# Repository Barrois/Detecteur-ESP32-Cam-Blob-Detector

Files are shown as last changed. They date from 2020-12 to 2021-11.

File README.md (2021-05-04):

# Detecteur-ESP32-Cam : Blob Detector Localisator

## Découpe des tâches à effectuer

- [x] [Détection acoustique du vol du frelon asiatique](./sketchbook/ESP_CAM_Audio_Detection): Vespa Velutina Nigrithorax (ESP32-Cam).

- [x] Détection et prise de photo du frelon asiatique en vol stationnaire en moins d'une seconde (ESP32-Cam).

- [x] Localisation d'un Blob dans une photo JPEG/jpg en 180ms pour une résolution 320x240 pixels (ESP32-Cam).

- [x] Détection de la tâche la plus sombre de l'image (ESP32-Cam).

- [x] Déduction coordonnées/angles des servos pour actionner un pan/tilt (ESP32-Cam).

- [x] Transmission de l'ordre de déplacement du pan/tilt: un angle pour chacun des deux servos du pan/tilt (ESP32-Cam).

- [x] [Réception/écoute du port série](./sketchbook/CoordonneesSerie) pour récupérer les valeurs des angles (Arduino 3.3V)

- [x] Déplacement des servos alimentés et controllés par PCA9695 (Arduino 3.3V)

- [x] Écoute du capteur d'obstacle laser (Arduino 3.3V)

- [x] Actionnement d'une électrovanne via relais (Arduino 3.3V)

- [ ] Assembler les sections correspondantes dans un programme pour l'ESP32-Cam

- [ ] Assembler les sections correspondantes dans un programme pour l'Arduino

- [ ] Tester en conditions réelles

- [ ] Corriger/adapter/améliorer/pleurer :D

## Présentation du projet

Après analyse des fréquences émises lors du vol stationnaire du frelon devant une ruche,
nous avons mis au point un filtre FFT qui donne satisfaction puisqu'il a permis de détecter des frelons dans 5 sites différents en France durant l'été 2020 : Limoux, Limoges, Toulouse, Nice et Caen.

Afin de valider le filtre acoustique, nous avons réalisé un programme s'executant sur un ESP32-Cam muni d'un micro (sur son unique entrée dispo ou presque: GPIO0) pour faire un photo de l'intrus, cette détection s'effectue en moins d'une seconde.

La prise de la photo, son analyse pour déduire la localisation du frelon est quant à elle réalisée en moins de 300ms (nb: en direct par l'ESP32-CAM).

### Principe d'analyse de l'image

L' analyse de la photo est basée sur le contraste et la taille d'une zone sombre (blob):

- La photo est prise depuis le dessus de la ruche en plongée devant un écran blanc.

- Les frelons, les abeilles et les résidus parsèment la photo et le pixel le plus noir n'est pas forcement la cible.

Toutefois en agglomérant des blocs de 4x4 pixels, on obtient des blobs dont le plus sombre est possiblement notre frelon:
plus gros qu'une abeille et plus noir/sombre qu'une feuille.

### Action !
Les coordonnées sont déduites de l'image et sont transmises à un Pan-Tilt guidé par un Arduino et équipé d'un dispositif de riposte (bille, eau, laser ...).

Il y a deux solutions en cours de recherche :

1.  Un ESP32-CAM détecte acoustiquement le Frelon asiatique, prend la photo en 320x240, l'analyse et transmet les coordonnées à un Arduino qui anime un Pan-Tilt équipé d'un laser. Actuellement c'est la solution explorée, la détection prend moins d'une seconde et la localisation 300ms.

2. un ESP32 équipé d'un Shield OV7670 et d'un Shield SD, détecte le frelon, prend la photo en 80x60, l'analyse et anime le Pan-Tilt équipé du laser.

Ce qui est fait :

- [x] la détection
- [x] la prise de photo
- [x] l'analyse et la localisation en pixel dans la photo

- [x] La détection par FFT et la sauvegarde sur carte SD : [ESP_CAM_timelapse_detector_Etienne_0.ino](./sketchbook/ESP_CAM_timelapse_detector_Etienne_0/ESP_CAM_timelapse_detector_Etienne_0.ino)

- [x] L'analyse en partant des photos mises en mémoires SPIFFS et la localisation du Blob : [decoder_jpeg_08_1.ino](./sketchbook/decoder_jpeg_08_1/decoder_jpeg_08_1.ino)

- [x] La prise de photo et l'analyse de blob grâce à l'excellent EloquentArduino :
https://github.com/eloquentarduino/EloquentArduino

et son example : https://eloquentarduino.github.io/2020/01/motion-detection-with-esp32-cam-only-arduino-version/

- [x] Une détection d'un blob 4x4 dans une photo 320x240 en 180ms !!! = : ESP32CameraNaiveMotionDetection_1.ino
- [x] envoyer et recevoir les coordonnées  de l'[ESP32-CAM à l'Arduino via Tx-Rx](./sketchbook/ESP_CAM_Audio_Detection)

Ce qu'il reste à faire :

- [ ] déclencher le tir du laser 10W alimenté en 12v 5A !!!
- [x] sauver la photo avec les coordonnées du tir pour la postérité.

La logique actuellement est la suivante :
- quand on allume l'esp32-cam
  1. il lit l'EEProm pour savoir à quel numéro de fichier il en est : xxx
  2. il fait une localisation qu'il sauvegarde sur la carte SD : fichier LOCAxxx.txt
  3. il fait une photo sauvegardée sur la carte SD : fichier CAPTURExxx.jpg
  4. il se met en position d'écoute sur le port 0
  5. il fait la FFT
  6. si le filtre de la FFT est positif, il commence à compter
  7. si le compteur du filtre atteint 5 reconnaissances en moins d'une seconde
        il collecte les 5 FFT qui ont déclenchées l'alarme et les stocke sur la carte SD : fichier FFTxxx.txt
        puis l'esp32-cam redémarre pour faire la localisation et la photo
  8. sinon il recommence en -4

Cette nouvelle version ["ESP_CAM_detector_localisor_Patrick_0_1"](./sketchbook/ESP_CAM_detector_localisor_Patrick_0_1/ESP_CAM_detector_localisor_Patrick_0_1.ino) (en hommage à Patrick DESSEAUX qui m'aide beaucoup)
marque un tournant dans la détection : après son analyse, seule la première harmonique est testée : 230Hz +/- 10%.

Et sans doute allons-nous modifier aussi le dispositif suivant son idée : un micro sur le devant de la ruche et un micro d'ambiance,
afin de supprimer les faux positifs dus à l'environnement (mobylette et autres..) et donc raccourcir le temps de détection.

## Le canon à bille de Ptilab: la solution la plus prometteuse !

Un canon a été experimenté avec succés par Ptitlab et son ami bbruno:

Depuis 2017 ils tirent le frelon :  https://drive.google.com/file/d/16ssjIsU98TqoQO_uRPv50JdfcAjg1aXl/view?usp=sharing

Plus de renseignements sur : http://ruchewarre.net/viewtopic.php?f=175&t=10218
Nous attendons beaucoup de cette collaboration.

Si vous avez des idées pour tuer les frelons asiatiques, merci de nous en faire part

Merci à tous

# Documentation

## Composants

[Liste des composants](documentation/Composants.md)

## Schema des connexions ESP32-Cam

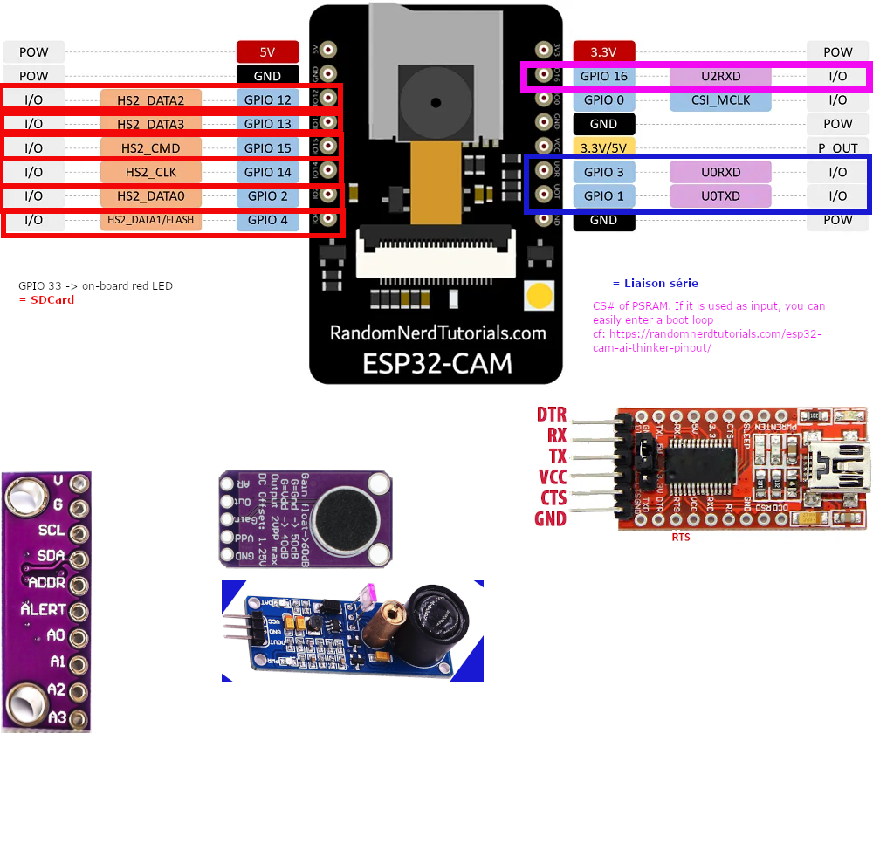
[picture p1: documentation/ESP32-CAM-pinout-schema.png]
SP32-CAM-pinout-schema


## Essais laser
[Essais laser](documentation/Laser.md)

## Quelques images capturées

### Frelons
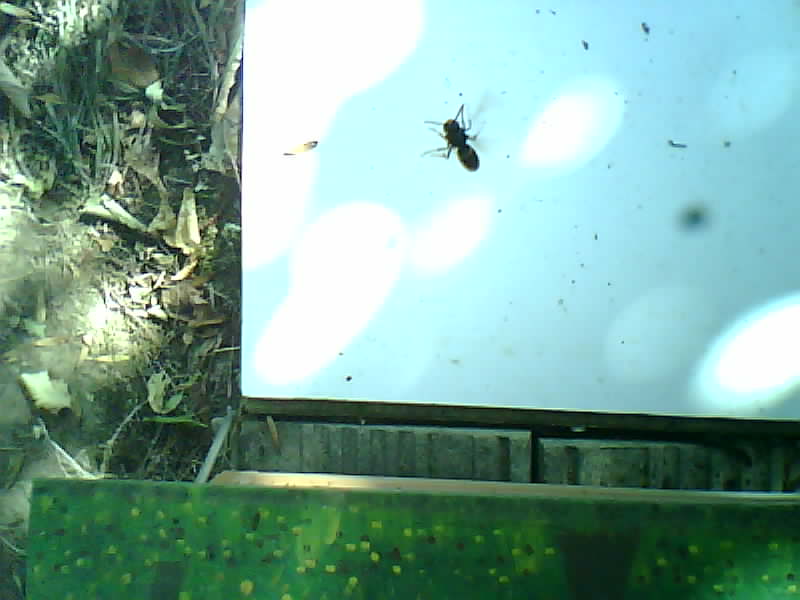
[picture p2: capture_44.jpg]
capture_44

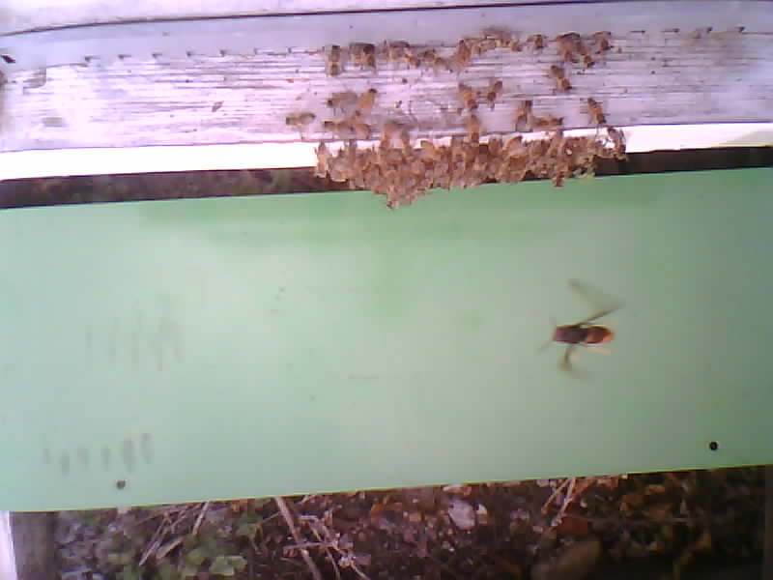
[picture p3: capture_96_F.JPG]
capture_96_F

capture_96_F

### Frelon ?
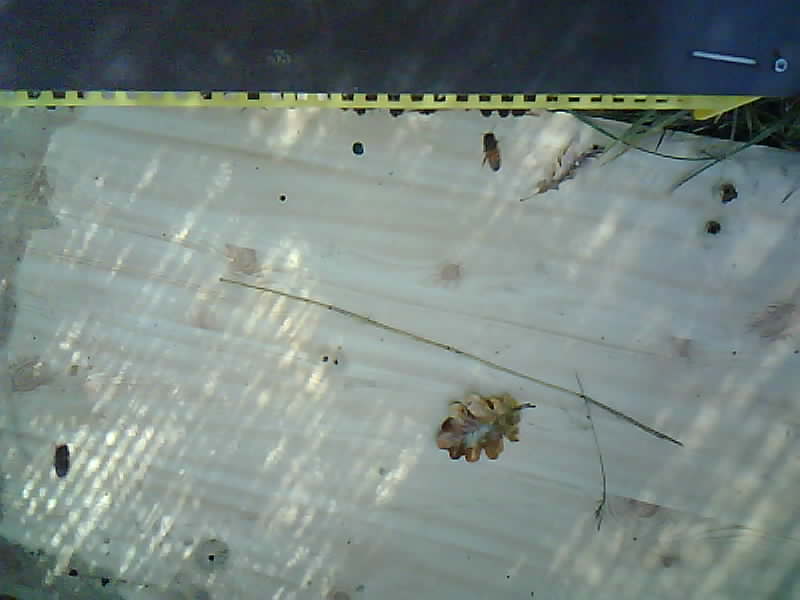
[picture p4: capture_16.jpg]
capture_16

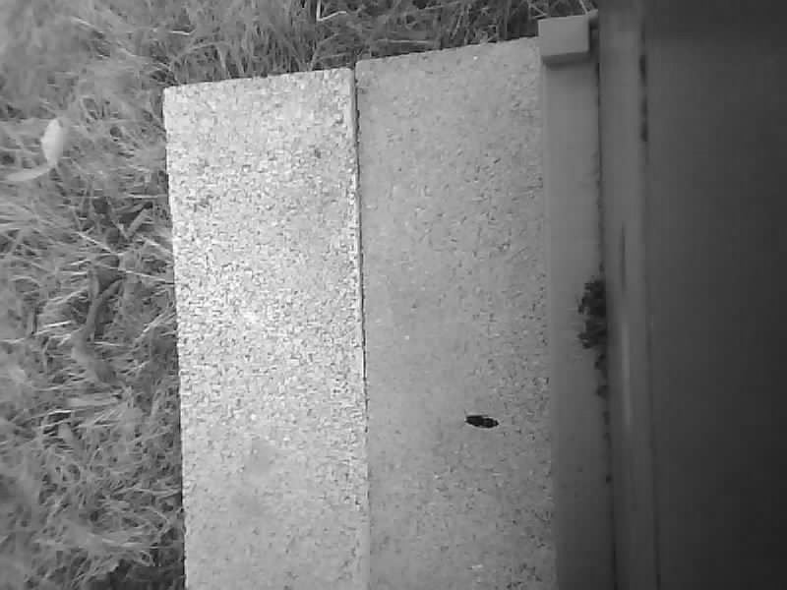
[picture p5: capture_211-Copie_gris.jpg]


## Enregistrements audio

[bruit_rue+frelon_1](Son-2019-08-16-09-39_bruit_rue+frelon_1.wav)

[bruit_rue+frelon_2](Son-2019-08-16-09-39_bruit_rue+frelon_2.wav)

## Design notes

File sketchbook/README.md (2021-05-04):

# Sketches de test

## Détection acoustique du vol de frelon

[Communication série](./CoordonneesSerie) de l'ESP32 vers Arduino (test côté Arduino)

[ESP_CAM_Audio_Detection](./ESP_CAM_Audio_Detection)

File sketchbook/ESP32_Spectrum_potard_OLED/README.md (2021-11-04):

# Détecteur acoustique de frelon pour ESP32

L'objectif est de faire un détecteur bas coût avec la possibilité d'ajuster la détection en fonction du frelon asiatique.
En effet le poids et la taille du frelon asiatique varient avec l'avancée de la saison et l'abondance de la nourriture,
ce qui entraine des variations du pic de détection qu'il faut pouvoir régler in situ, d'ou ce montage avec un potentiomètre.
L'affichage sur un écran permet de visualiser les valeurs de la fréquence la plus élevée (pic), celle du potentiomètre ainsi
qu'un message lors d'une détection.

## Pré requis

- Installation de la carte ESP32 dans l'IDE Arduino (cf: https://randomnerdtutorials.com/installing-the-esp32-board-in-arduino-ide-windows-instructions/)
- Installation de la librairie ArduinoFFT (https://github.com/kosme/arduinoFFT) depuis le getionnaire de librairies de l'IDE Arduino
- Installation de la librairie Adafruit_GFX_Library (Affichage écran OLED)
- Installation de la librairie Adafruit_SSD1306 (Affichage écran OLED)

## Raccordements

- le potentiomètre de règlage de la valeur du pic de fréquence est relié au GPIO 32, ADC1_CH4 (cf: potardPin 32)

- le micro (ici type MAX9814) est relié sur le GPIO 33, ADC1_CH5 (cf: microPIN 33)

- un écran OLED de 128x32 pixels en I2C sur GPIO 26 (PIN_SDA) et GPIO 27 (PIN_SCL);

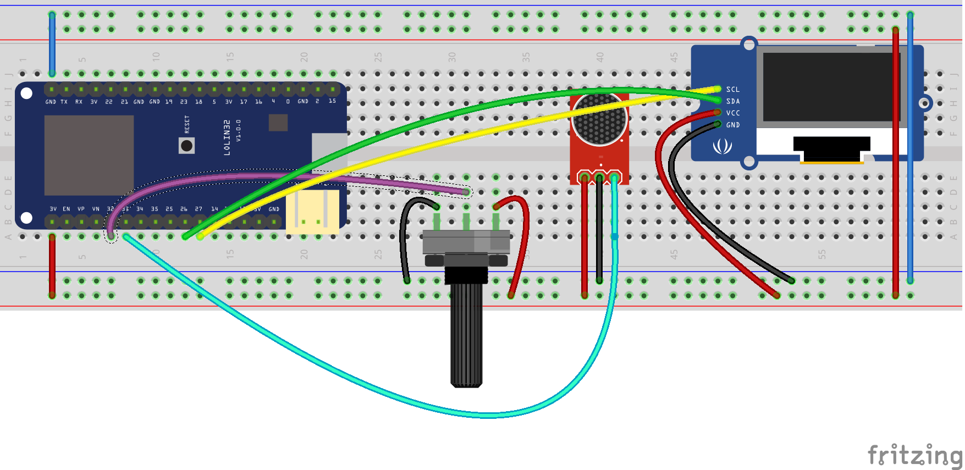
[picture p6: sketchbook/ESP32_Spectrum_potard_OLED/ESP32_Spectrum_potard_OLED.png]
Schema Breadboard

## Détection

Le potentiomètre permet de varier de 100 à 1000 Hz la fréquence de détection.

cf ligne 103, 4095 étant la valeur maximale de l'ADC, 100 correspond à 0 et 1000 à 4095:
```
int range = map(adc0, 0, 4095, 100, 1000);
```

la féquence de référence devrait se situer aux alentours de 230.

Il semblerait toutefois que les harmoniques soient plus facilement détectables.

Sans avoir vraiment d'explication, la fréquence 460 fonctionne mieux avec l'esp8266 que 230, et 920 pour l'ESP32.

À vérifier en "conditions réelles".

En cas de détection la led de la carte est allumée (variable LED_BUILTIN qui doit dépendre du type de carte sélectionnée dans l'IDE Arduino > Outils > Type de carte).

Sur l'ESP32 Lolin32 Lite servant aux essais, la logique est inversée: HIGH éteint la led et LOW l'allume, il faudra peut être inverser la logique sur une autre carte.

## Fichier de test

https://github.com/Jodaille/VespaVelutinaAudioRecords/blob/main/complets/2020-09-23-092858.ogg?raw=true

Avec 920 de valeur, en écoutant via un PC et Audacity en ajustant un peu le niveau, le frelon est détecté. Après le Koutish de la raquette de badmington, le frelon est au sol battant des ailes, la détection tout de même :-)

d'autres fichiers sont disponibles:

https://github.com/Jodaille/VespaVelutinaAudioRecords/tree/main/complets

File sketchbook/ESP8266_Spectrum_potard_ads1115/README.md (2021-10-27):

# Détecteur acoustique de frelon pour ESP8266

L'objectif est de faire un détecteur bas coût avec la possibilité d'ajuster la détection en fonction du frelon asiatique.
En effet le poids et la taille du frelon asiatique varient avec l'avancée de la saison et l'abondance de la nourriture,
ce qui entraine des variations du pic de détection qu'il faut pouvoir régler in situ, d'ou ce montage avec un potentiomètre

## Pré requis

- Installation de la carte ESP8266 dans l'IDE Arduino (cf: https://randomnerdtutorials.com/how-to-install-esp8266-board-arduino-ide/)
- Installation de la librairie ArduinoFFT (https://github.com/kosme/arduinoFFT) depuis le getionnaire de librairies de l'IDE Arduino
- Installation de la librairie Adafruit_ADS1X15 https://github.com/adafruit/Adafruit_ADS1X15

## Raccordements

- le micro est relié au seul ADC de l'esp8266, à savoir ADC0/A0
- le relais est relié sur la sortie D1, sauf que D1 est aussi SCL de l'I2C (D2 pour SDA)
il ne peut donc être enfiché directement sur les headers de l'ESP8266
- l'ESP8266 ne dispose que d'un ADC (A0), pour utiliser le potentiomètre de règlage de la valeur du pic de fréquence, nous utilisons un ADS1115 en I2C (D1 et D2)

## Schéma breadboard avec Fritzing

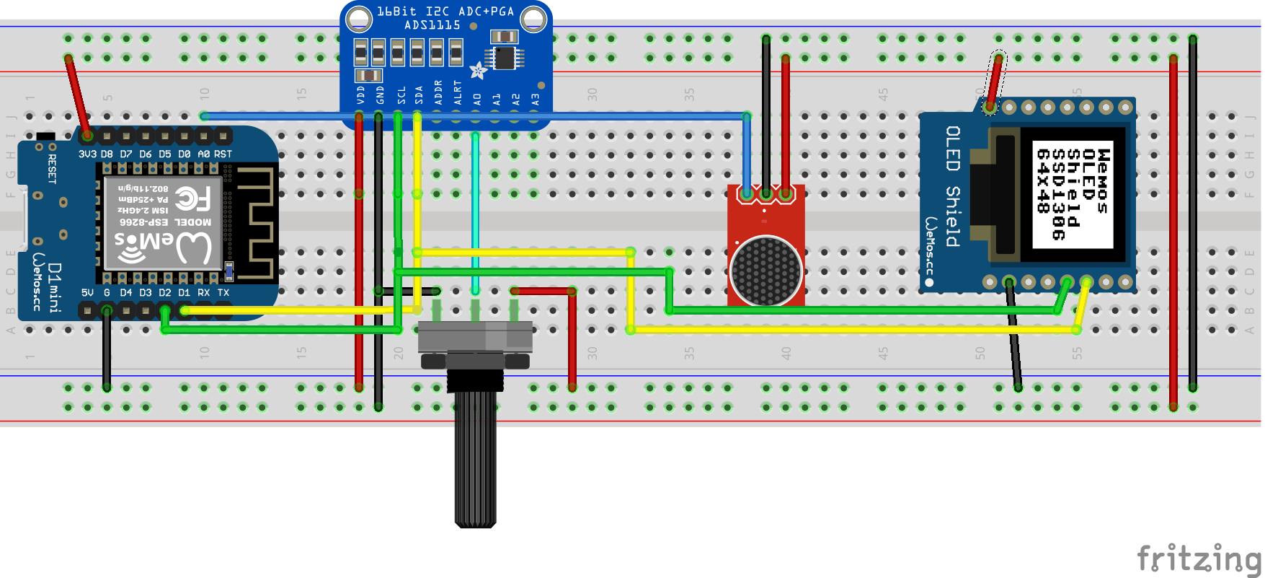
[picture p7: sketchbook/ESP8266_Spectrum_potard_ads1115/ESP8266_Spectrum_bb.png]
Schema Breadboard


Le circuit de test sur breadboard :
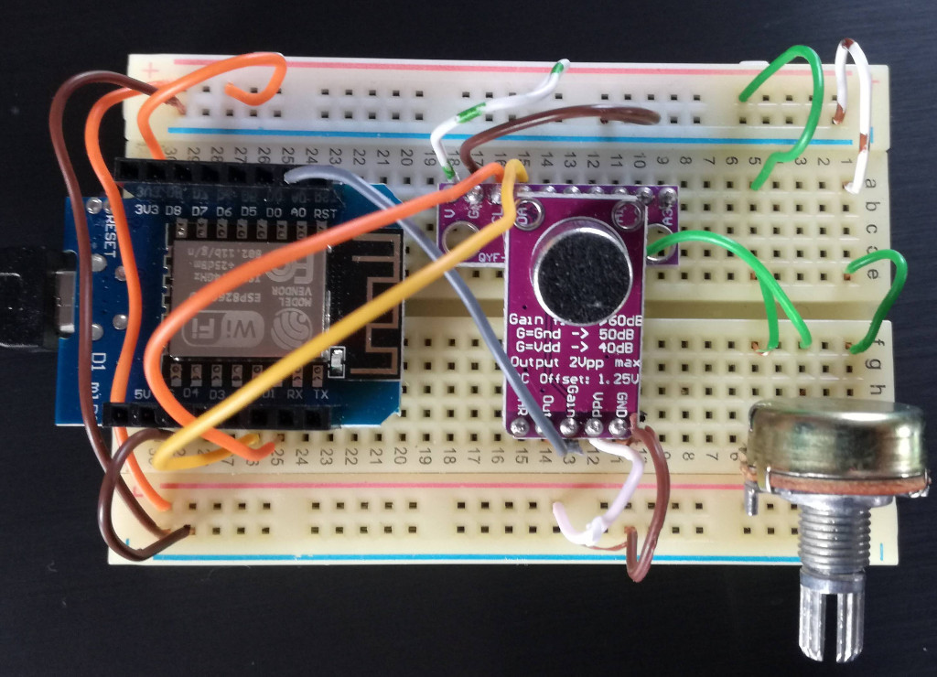
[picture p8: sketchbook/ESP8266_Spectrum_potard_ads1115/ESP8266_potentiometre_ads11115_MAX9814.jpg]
Circuit sur Breadboard


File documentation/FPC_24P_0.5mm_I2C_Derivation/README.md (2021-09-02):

# Déviation du bus I2C de l'Esp32-Cam avec deux plaques FPC 24P 0.5mm

Utilisation de headers mâles 2.54mm

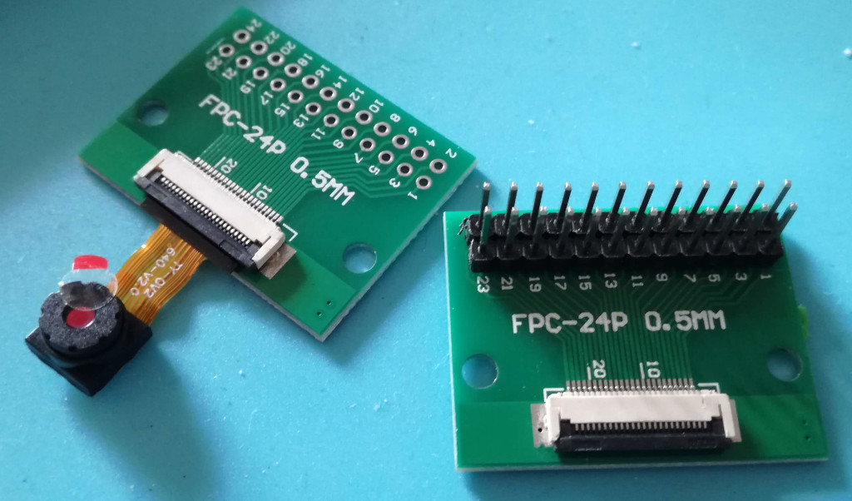
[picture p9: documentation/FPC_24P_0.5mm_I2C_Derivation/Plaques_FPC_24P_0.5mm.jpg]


Les deux plaques FPC 24P 0.5mm assemblées:

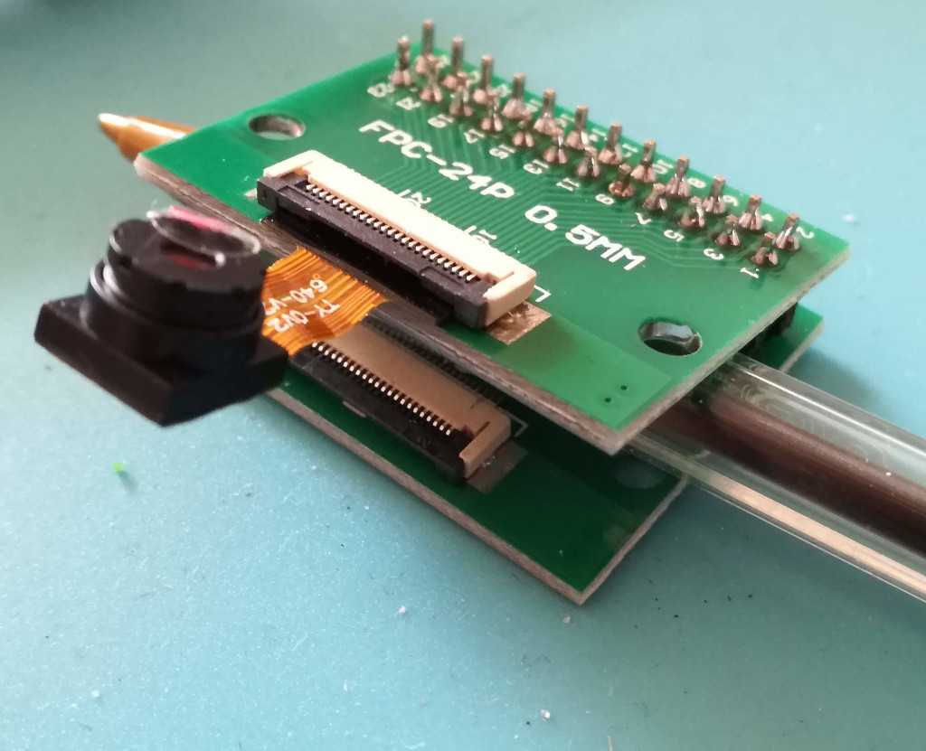
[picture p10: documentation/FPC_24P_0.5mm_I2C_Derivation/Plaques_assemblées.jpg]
Plaques assemblées Deux plaques FPC assemblées


Les plaques, la nappe, la caméra et l'ESP32-Cam

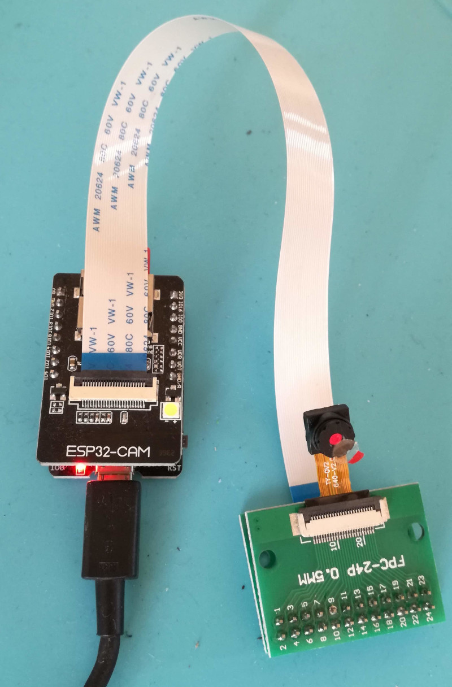
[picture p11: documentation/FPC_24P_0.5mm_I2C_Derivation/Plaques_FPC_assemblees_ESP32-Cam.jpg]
Les plaques, la nappe, la caméra et l'ESP32-Cam


Les connecteurs pour l'I2C:

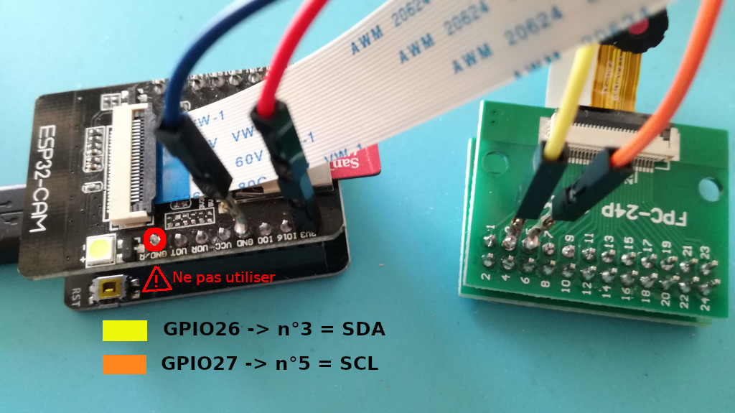
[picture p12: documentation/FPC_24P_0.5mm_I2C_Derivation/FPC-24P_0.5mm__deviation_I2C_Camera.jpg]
schéma SDA et SCL


## Exemple d'utilisation du bus I2C: scanner

```
#include <Wire.h>

const int PIN_SDA = 26;  // port 26 du esp32-cam sur le SDA directement sur la puce
const int PIN_SCL = 27;  // port 27 du esp32-cam sur le SCL directement sur la puce
void setup()
{
  Serial.begin(115200);
  Wire.begin(PIN_SDA, PIN_SCL);
}

void loop()
{
  byte error, address;
  int nDevices;

  Serial.println("Scanning...");

  nDevices = 0;
  for(address = 1; address < 127; address++ ) {
    // The i2c_scanner uses the return value of
    // the Write.endTransmisstion to see if
    // a device did acknowledge to the address.
    Wire.beginTransmission(address);
    error = Wire.endTransmission();

    if (error == 0) {
      Serial.print("I2C device found at address 0x");
      if (address<16) {
        Serial.print("0");
      }
      Serial.print(address,HEX);
      Serial.println("  !");
      nDevices++;
    }
    else if (error==4) {
      Serial.print("Unknow error at address 0x");
      if (address<16){
        Serial.print("0");
      }
      Serial.println(address,HEX);
    }
  }
  if (nDevices == 0) {
    Serial.println("No I2C devices found\n");
  }
  else {
    Serial.println("done\n");
  }
  delay(5000);           // wait 5 seconds for next scan
}
```

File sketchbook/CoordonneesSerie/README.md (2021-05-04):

# Test de passage de paramètres via le port série

## Utilisation de la virgule en tant que délimiteur

Afin de pouvoir indiquer les angles X (pan) et Y (tilt) aux deux servos,

nous projetons d'écrire ces coordonnées sur le port série depuis l'ESP32 vers l'Arduino.

Example pour X à 125° et Y à 145°
````
Serial.println("125,145")
````

## Passage d'un id de commande

Pour permettre un ajout d'autres paramètres (dans le futur), ou d'une autre action.

Nous ajoutons en premier paramètre un id de commande, la valeur 1 sera "déplacement des servos"

ainsi l'ESP32 enverra en premier la valeur 1, pour un ordre type "déplacement de servos":

Example pour X à 125° et Y à 145°
````
Serial.println("1,125,145")
````

## Tester depuis le moniteur série

Une fois le sketch chargé, il est possible de tester en indiquant dans le moniteur série, dans le prompt en haut de la fenêtre la chaîne de caractère suivante, suivi d'une validation par la touche Entrée:

````
1,24,67
````

le message en retour devrait être:

````
captured String is : 1,24,67
command = 1 / angleX = 24 / integerAngleX = 24
integerCommand = 1 / angleY = 67 / integerAngleY = 67
Deplacement du servo !
````

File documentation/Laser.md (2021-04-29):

# Laser ou pas laser

## Essais d'un laser

5.5w haute puissance 445NM focalisation module laser bleu gravure laser et découpe module TTL tube laser 5500mw

Description du produit :

- Longueur d'onde: 445NM
- Puissance: 5.5W (max. 4.8w)
- Courant électrique: entrée 3-5A
- Tension: DC 12V
- Température de fonctionnement: + 10 ~ + 40
- Module de pilote: TTL
- Mise au point Laser réglable
- Taille: 33*33*75mm

Possible de brûler du bois à près de 80cm en ajustant la "focale" (pas sûr du terne)

Toutefois pas d'instantaéité, il faut laisser le faisceau quelques secondes pour brûler.

En calant à peu près la focale (lorsqu'elle brûle du bois), j'ai essayé de toucher une grosse mouche,
celle-ci s'est envolée à peine en contact avec le faisceau.

## Pour

- Pas de projectile à ramasser

- Pas de projectile à recharger/débloquer

## Contre
- Illégalité: https://www.ecologie.gouv.fr/lutte-contre-lusage-des-lasers-dans-transport-aerien

- risque d'incendie

- risque de brûlure notamment des yeux !

- consommation électrique

- efficacité non démontrée

## Illustration

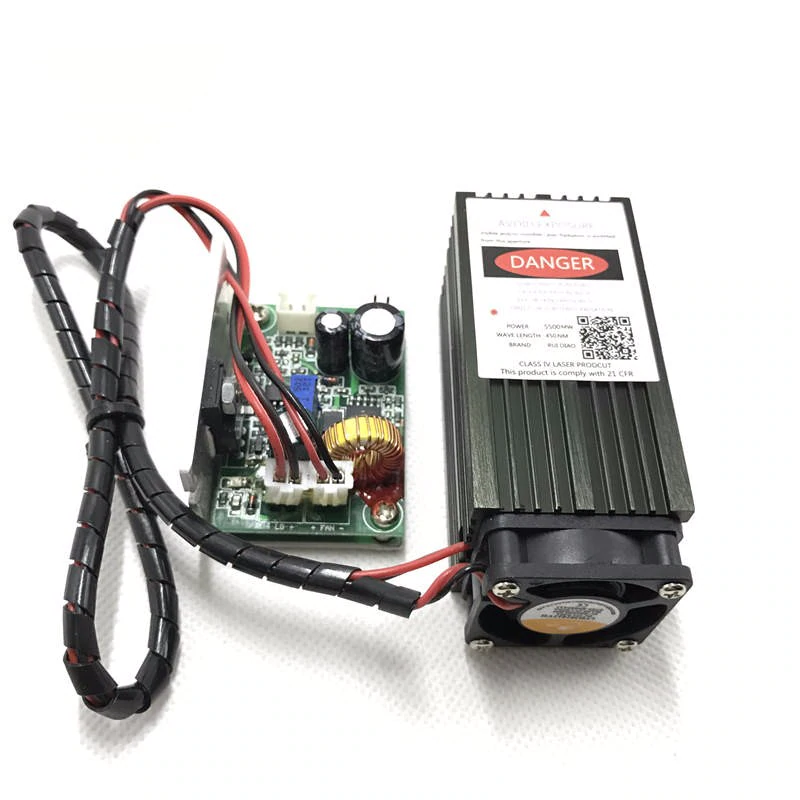
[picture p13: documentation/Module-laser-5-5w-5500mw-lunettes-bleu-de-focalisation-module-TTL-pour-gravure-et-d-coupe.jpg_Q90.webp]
module-laser-5-5w-5500mw


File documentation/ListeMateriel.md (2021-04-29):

Voici le matériel requis pour faire la partie détection-localisation

    un esp32-cam (objectif standard)
    une carte mémoire micro SD
    un module de chargement FTDI ou équivalent
    un micro MAX9814 ou équivalent (fabriqué par Michel) mais qui ne génére pas de GND sur le port zéro de l'esp32-Cam au départ
    une alimentation 5 volts 1A (2 c'est mieux)

Voici le matériel requis pour faire la partie canon (à air et bille ou à liquide, électromagnétique à clou ou goupille)

    un canon tel que désiré : à air et bille ou à liquide, électromagnétique à clou ou goupille
        pour le canon à air prévoir les électrovannes, les tuyaux, et la réserve d'air (vase d'expansion par exemple)
        et le STL de la culasse utilisé.
        pour le canon à liquide prévoir ... ce qu'il faut ... vanne, tuyau, etc...
        et le STL de la culasse utilisé.
        pour le canon électromagnétique prévoir l'alimentation spécifique à la bobine et son condensateur
        et le STL de la culasse utilisé.
    un Pan-Tilt
    deux servo-moteur 5V costauds pour la maneouvre du canon
    un servo-moteur 5V pour la gachette du canon ou l'armenemt suivant le cas
    une relais 12V pour les électrovannes si nécessaire
    un PCA9685 pour gérer les servo-moteurs et leur alimentation
    un viseur électronique : module LASER d'Adafruit ou son équivalent fabriqué par Michel
    un arduino mini pro ou nano de préférence en 3.3 volts
    un ads1115 (facultatif)
    un écran Oled (facultatif)
    une alimentation 5 volts 2A pour l'arduino
    une alimentation 12v pour les électrovannes si nécessaire

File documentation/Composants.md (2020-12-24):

# Detecteur-ESP32-Cam

## Composants

- un ESP32-CAM

- un micro type Max9814

- (une carte Sd)

- un interrupteur pour l'alimentation

- un interrupteur pour désactiver la sortie du micro au démarrage de l'ESP32 (port GPIO0 utilisé pour passer en mode flash)

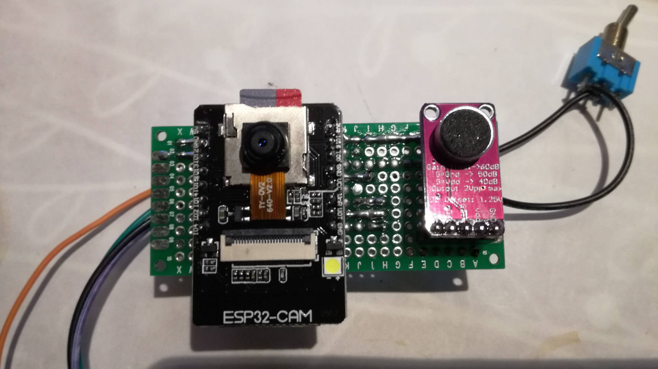
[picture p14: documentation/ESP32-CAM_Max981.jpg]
ESP32-CAM et micro Max981


## Montage

La sortie du Max9814 est reliée sur l'entrée GIPO0 de l'ESP32-CAM.

Un interrupteur permet de déconnecter les deux au démarrage de l'ESP-32 afin qu'il ne passe pas en mode "flash".

## Idées de boitier "étanches"

exemple d'utilsation boîte de dérivation:

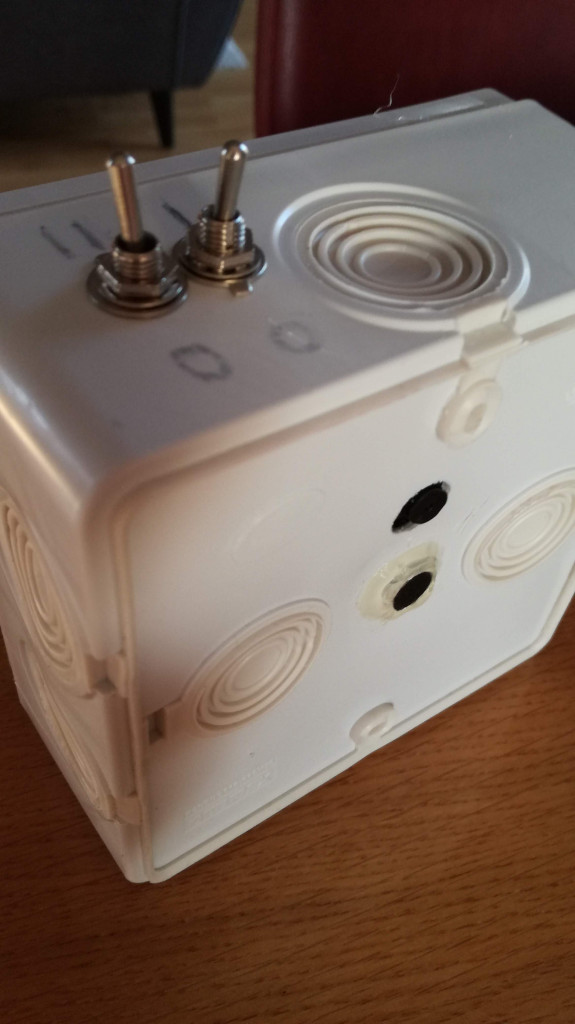
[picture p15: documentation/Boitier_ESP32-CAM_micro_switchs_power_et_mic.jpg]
Boitier_ESP32-CAM_micro_switchs


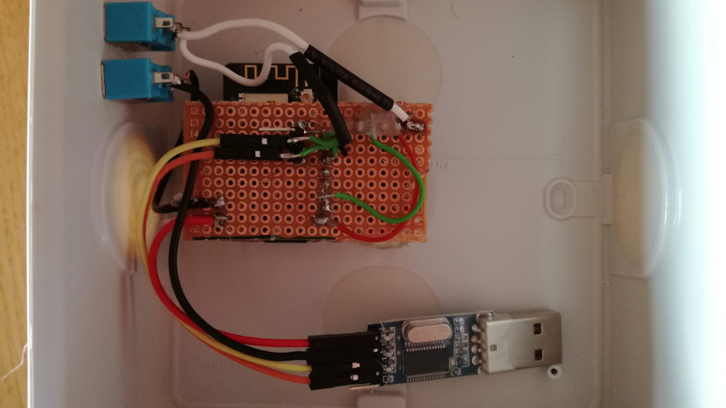
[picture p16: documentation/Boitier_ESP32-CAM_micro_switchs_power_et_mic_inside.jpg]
Boitier_ESP32-CAM_micro_switchs


## Autres info./outils

### Entrée audio pour ESP-32: schéma

l'idée serait de pouvoir jouer un enregistrement audio d'un vol de frelon afin de tester l'algo/filtre de détection

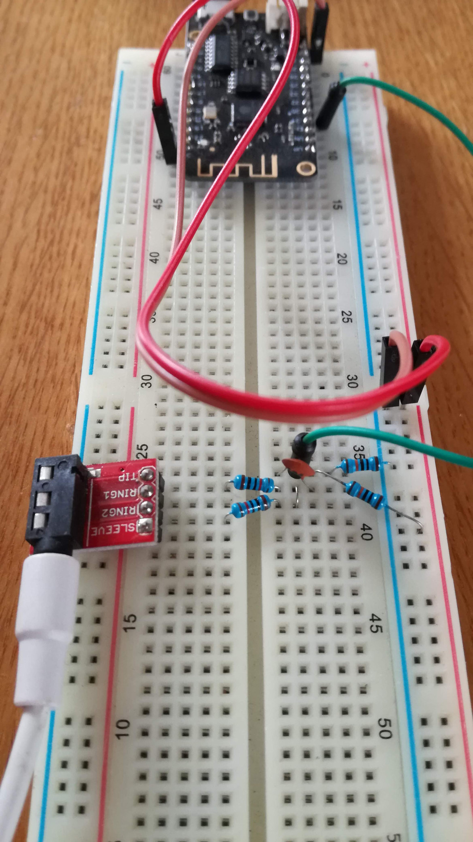
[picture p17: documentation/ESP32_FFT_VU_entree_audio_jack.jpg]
ESP32_FFT_VU_entree_audio_jack


cf: https://github.com/s-marley/ESP32_FFT_VU/blob/master/Linein_bb.png

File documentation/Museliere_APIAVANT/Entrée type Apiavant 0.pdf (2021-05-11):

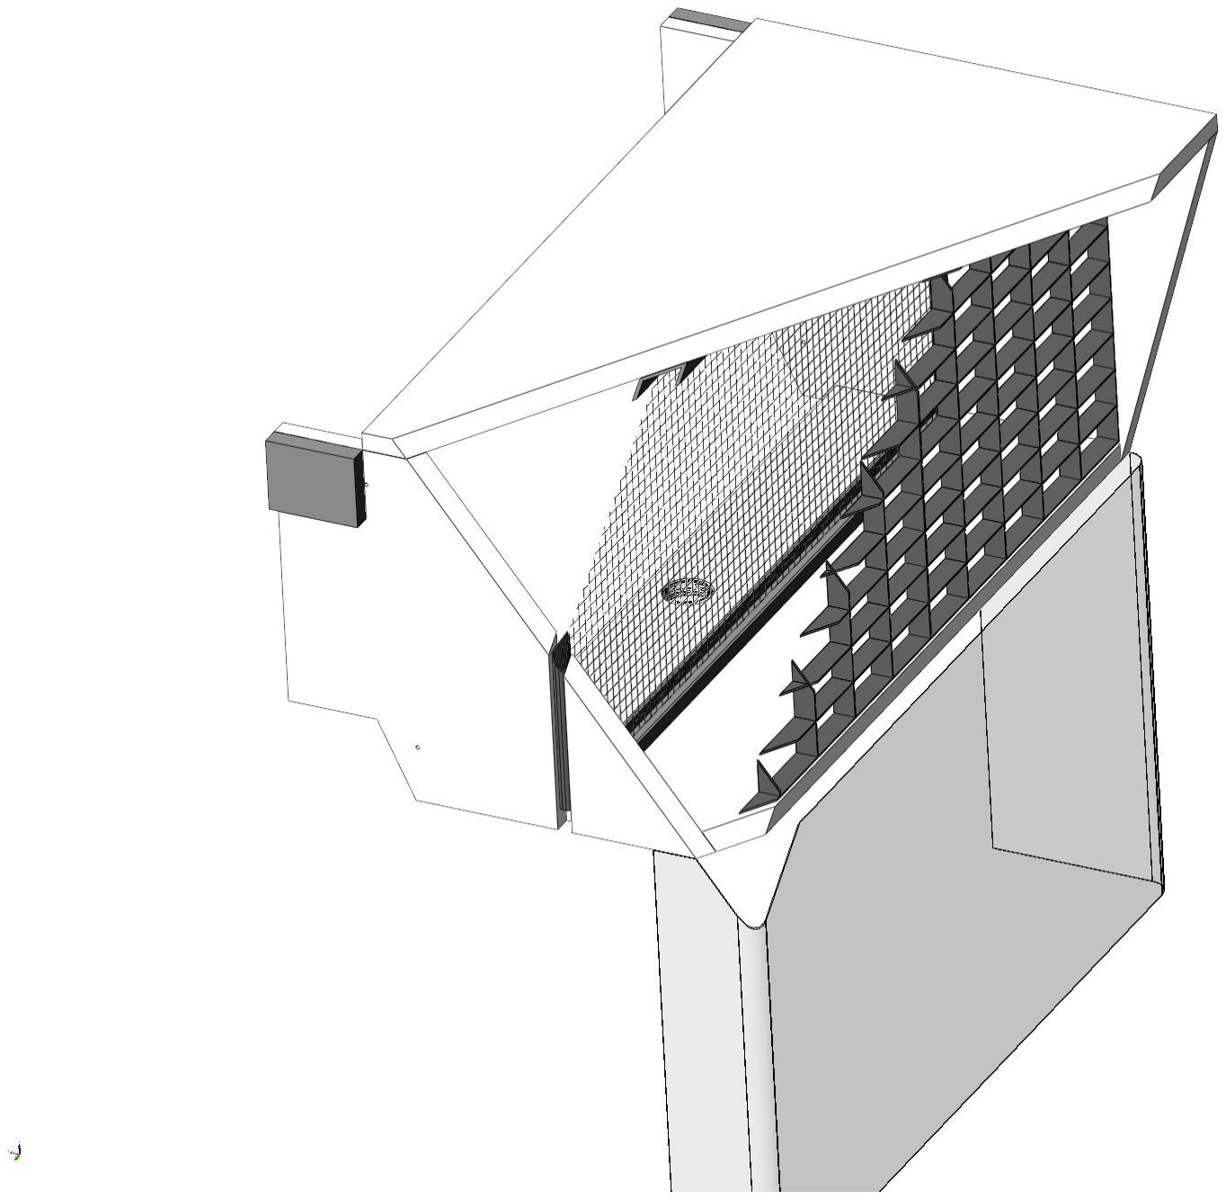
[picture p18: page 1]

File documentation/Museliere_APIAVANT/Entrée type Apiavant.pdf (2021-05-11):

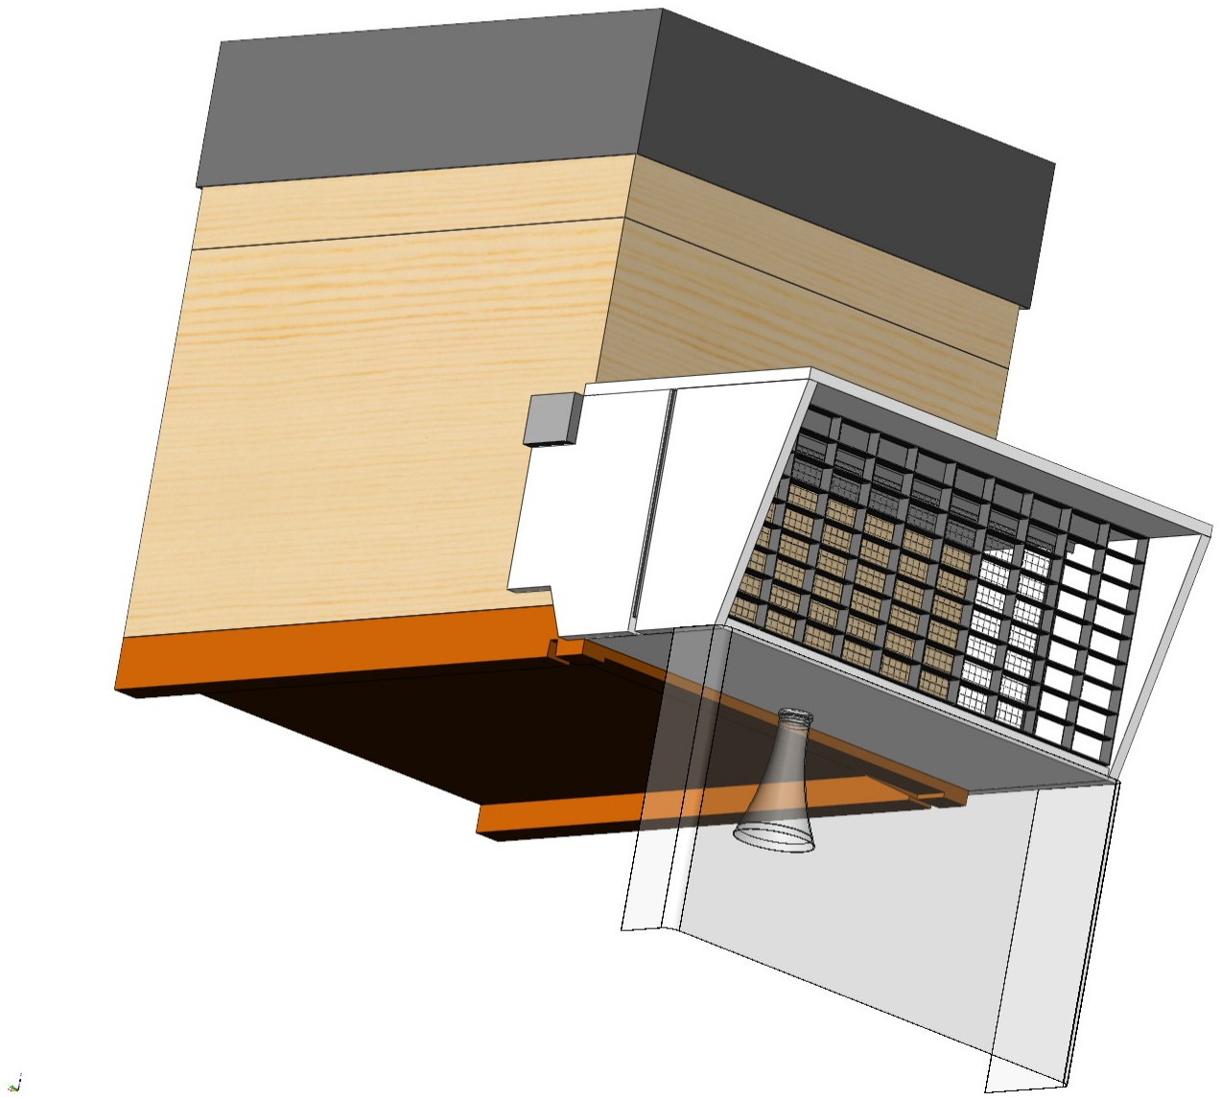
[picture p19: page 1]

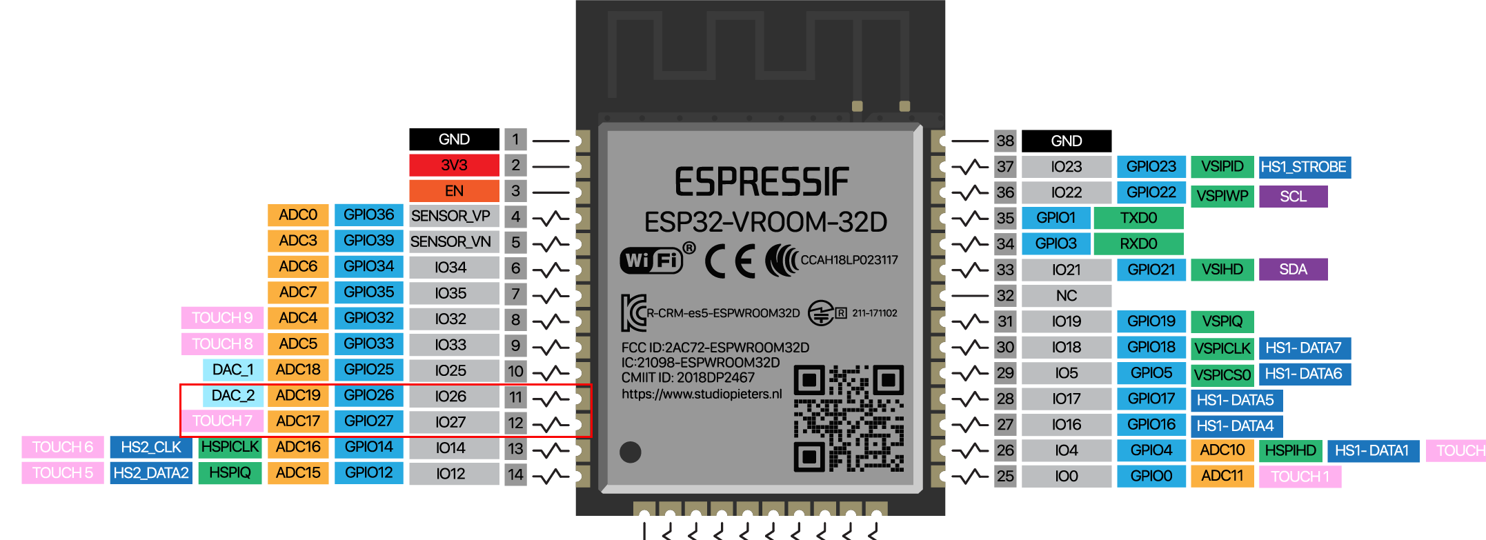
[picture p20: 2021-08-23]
documentation/ESP32-VROOM-32D-PINOUT_I2C.png

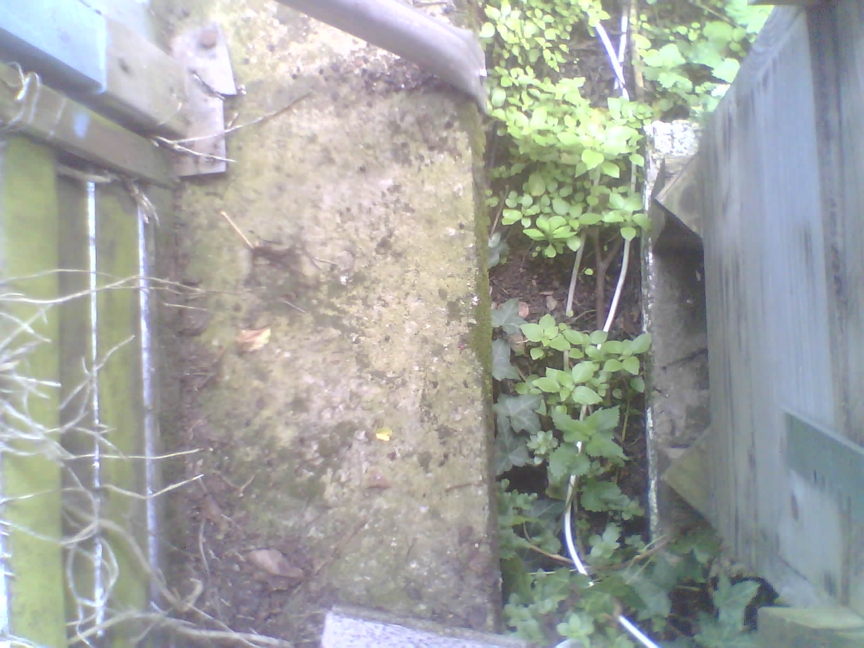
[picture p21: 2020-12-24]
capture_18.jpg

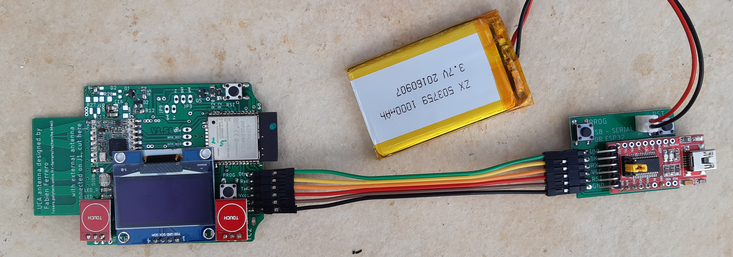
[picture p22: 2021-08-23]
documentation/module-ftdi.png

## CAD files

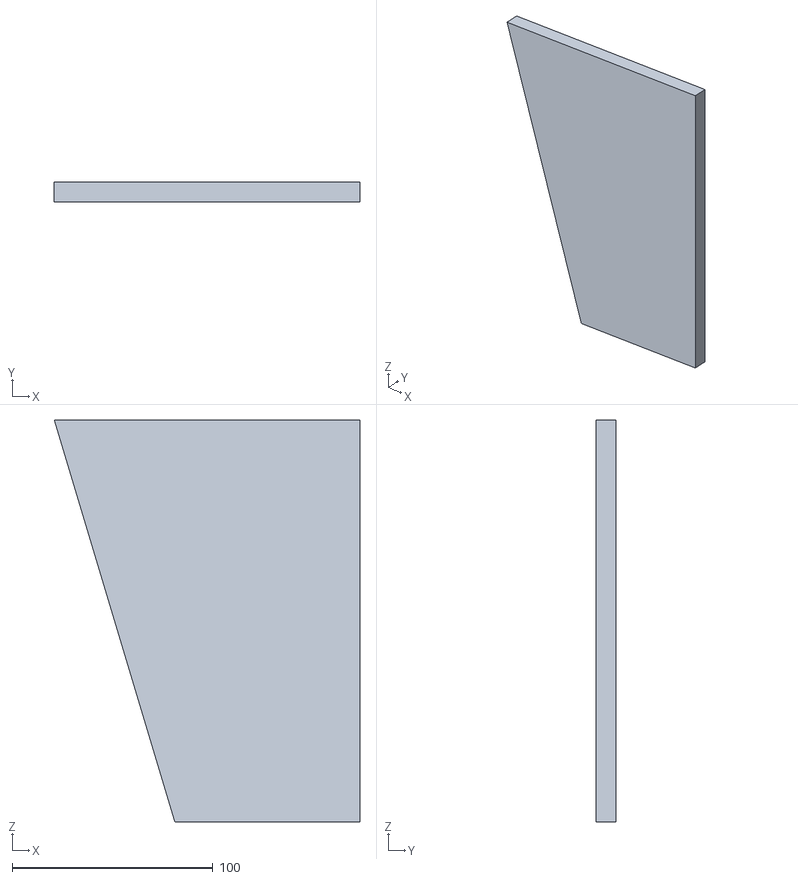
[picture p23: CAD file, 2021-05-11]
documentation/Museliere_APIAVANT/Protection plancher Nicot beelaz V3 - Lat B^Protection plancher Nicot beelaz V3-1.STL
152.0 x 10.0 x 200.0

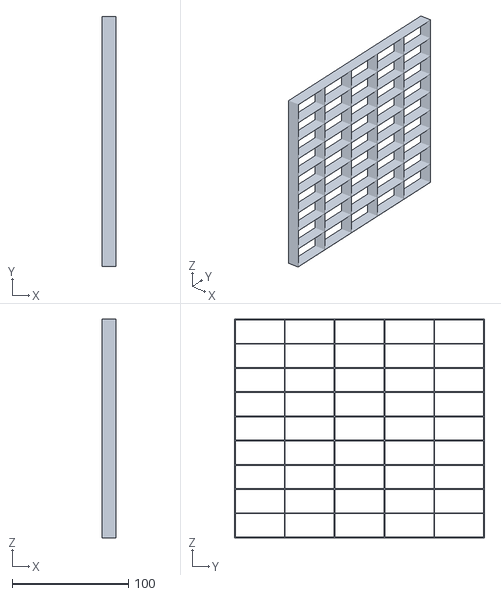
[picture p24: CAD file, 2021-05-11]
documentation/Museliere_APIAVANT/Protection plancher Nicot beelaz V3 - Grille d'entrée allégée^Protection plancher Nicot beelaz V3-2.STL
12.0 x 214.8 x 188.0

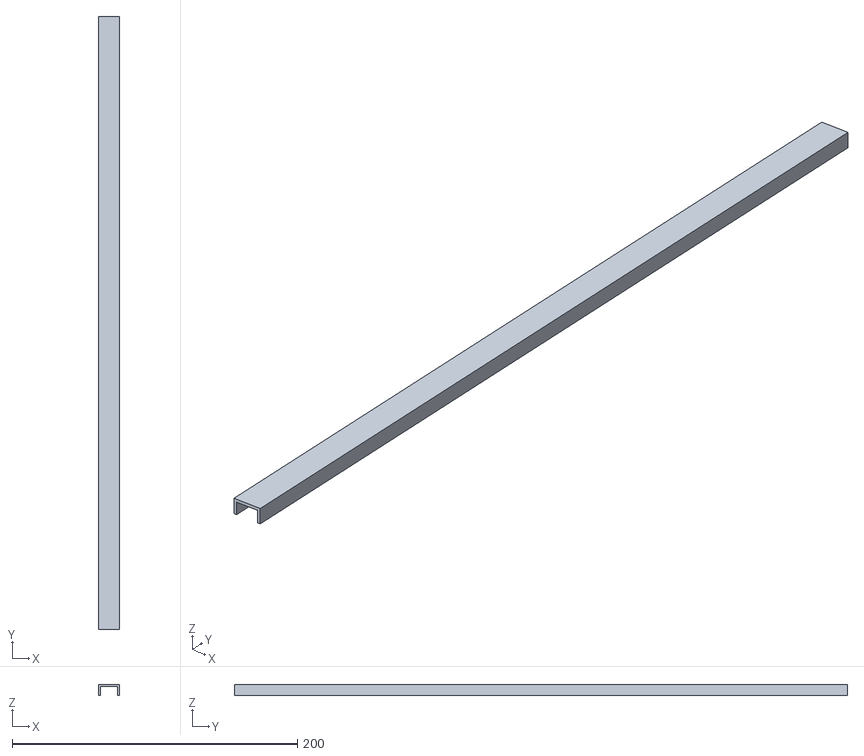
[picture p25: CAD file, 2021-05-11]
documentation/Museliere_APIAVANT/Protection plancher Nicot beelaz V3 - U LR 15x8x1_5^Protection plancher Nicot beelaz V3-2.STL
15.0 x 430.0 x 8.00

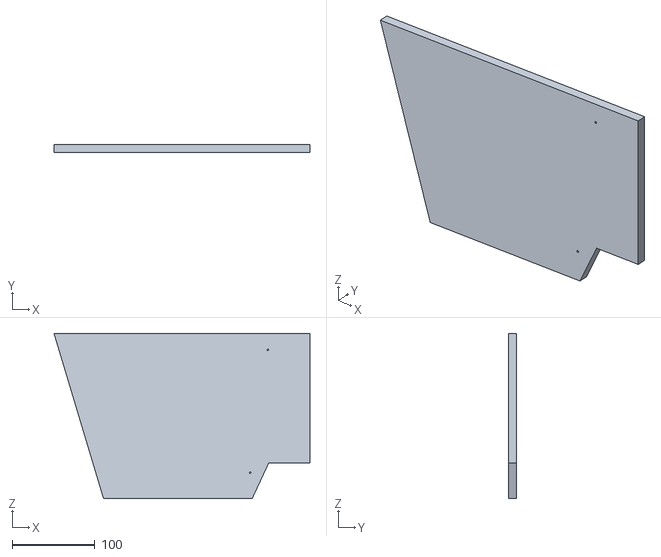
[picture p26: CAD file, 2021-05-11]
documentation/Museliere_APIAVANT/Protection plancher Nicot beelaz V3 - Lat A^Protection plancher Nicot beelaz V3-1.STL
310.0 x 10.0 x 200.0

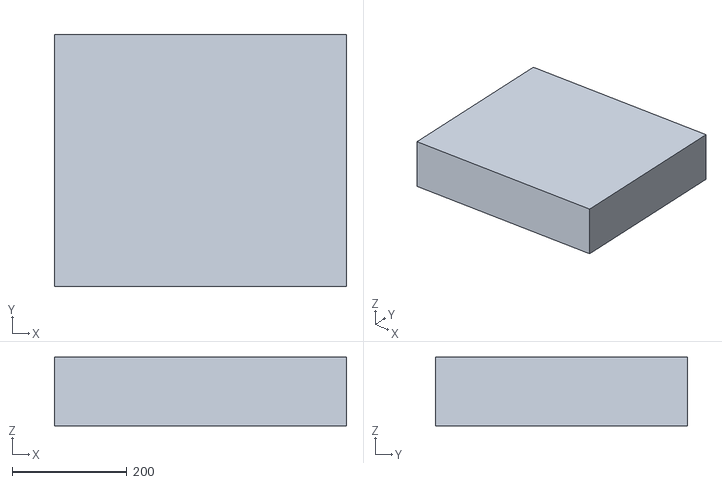
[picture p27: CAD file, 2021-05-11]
documentation/Museliere_APIAVANT/Protection plancher Nicot beelaz V3 - Capot^Protection plancher Nicot beelaz V3-1.STL
510.0 x 440.0 x 120.0

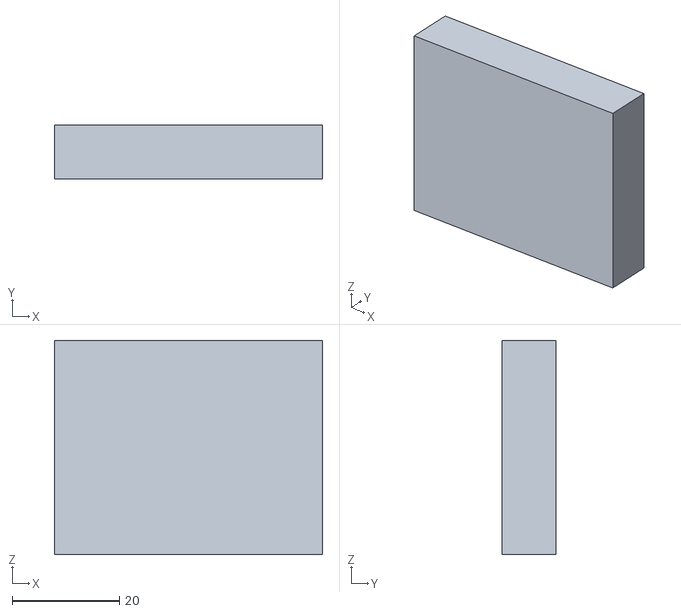
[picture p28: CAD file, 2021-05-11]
documentation/Museliere_APIAVANT/Protection plancher Nicot beelaz V3 - Cale 50x40x10^Protection plancher Nicot beelaz V3-6.STL
50.0 x 10.00 x 40.0

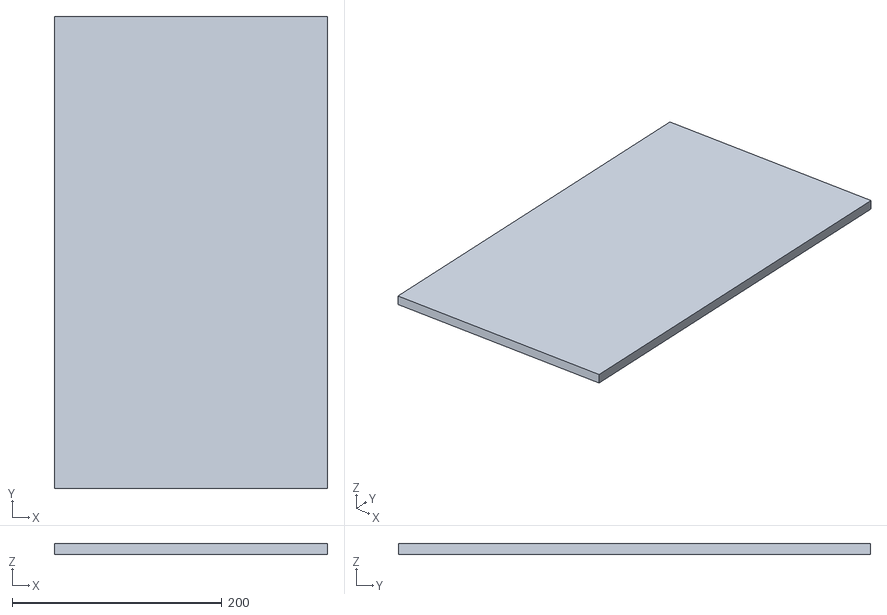
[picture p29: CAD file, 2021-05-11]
documentation/Museliere_APIAVANT/Protection plancher Nicot beelaz V3 - Dessus^Protection plancher Nicot beelaz V3-1.STL
260.0 x 450.0 x 10.0

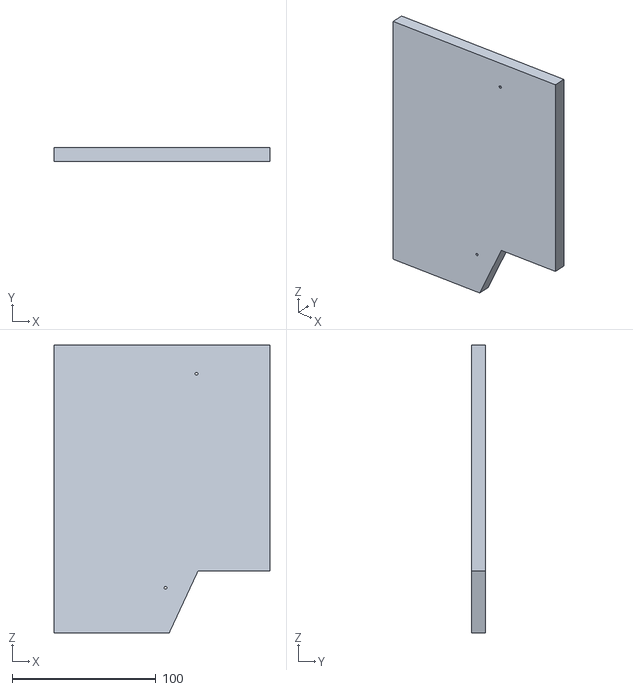
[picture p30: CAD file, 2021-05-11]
documentation/Museliere_APIAVANT/Protection plancher Nicot beelaz V3 - Lat C^Protection plancher Nicot beelaz V3-1.STL
150.0 x 10.0 x 200.0

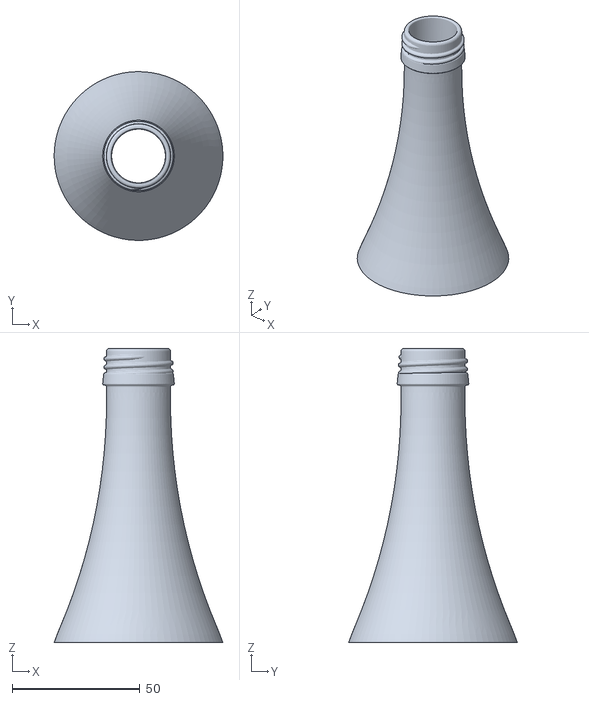
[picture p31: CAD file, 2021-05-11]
documentation/Museliere_APIAVANT/Protection plancher Nicot beelaz V3 - Bouteille eau coupée-1.STL
65.9 x 65.9 x 114.8

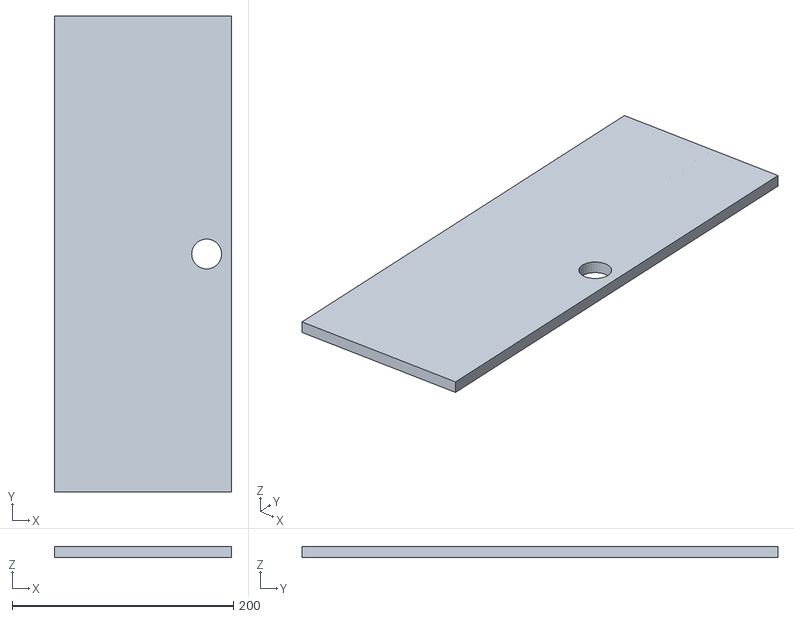
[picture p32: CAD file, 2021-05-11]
documentation/Museliere_APIAVANT/Protection plancher Nicot beelaz V3 - Plancher^Protection plancher Nicot beelaz V3-1.STL
160.0 x 430.0 x 10.0

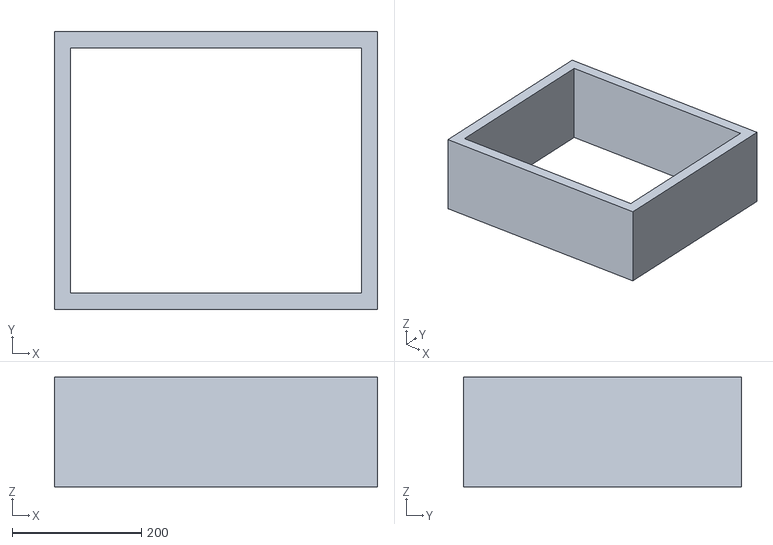
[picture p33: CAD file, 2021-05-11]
documentation/Museliere_APIAVANT/Protection plancher Nicot beelaz V3 - Copie de Ruche Dadant^Protection plancher Nicot beelaz V3-1 Hausse^Copie de Ruche Dadant_Protection plancher Nicot beelaz V3-1.S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
500.0 x 430.0 x 170.0

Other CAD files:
documentation/Museliere_APIAVANT/Protection plancher Nicot beelaz V3 - Grille d'entrée allégée^Protection plancher Nicot beelaz V3-1.STL
documentation/Museliere_APIAVANT/Protection plancher Nicot beelaz V3 - Cale 50x40x10^Protection plancher Nicot beelaz V3-8.STL
documentation/Museliere_APIAVANT/Protection plancher Nicot beelaz V3 - U LR 15x8x1_5^Protection plancher Nicot beelaz V3-1.STL

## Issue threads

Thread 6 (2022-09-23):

Question: usage de I2C

Patriboom, 2022-09-23:
Bonjour,

je comprends que vous avez pu combiner la pise d'image par la caméra ESP32 - AI Thinker à des capteurs I2C.

Est-ce que la déviriation de la caméra fut nécessaire à cela ?

Quelles broches utilisez-vous pour connecter les SDA et SCL des composants I2C ?

Je n'avais jamais imaginé que les adresses des GPIO devaient référer aux broches de la puce principal, mais c'est plein de bon sens.

Merci de votre aide.

Jodaille, 2022-09-23:
Bonjour,

à priori SDA et SCL ne sont accessibles que sur le connecteur de la caméra.

pour la dérivation via la nappe de la camera:
https://github.com/Barrois/Detecteur-ESP32-Cam-Blob-Detector/tree/main/documentation/FPC_24P_0.5mm_I2C_Derivation

Bernard pourra confirmer, les connexions caméra/i2c fonctionnent, il restait la partie initialisation/énumération de la caméra sur le bus. Il me semble que lorsque la caméra s'initialise au démarrage de la carte, le "sketch" prends en gros le premier périhpérique sur le bus I2C. De mémoire Bernard avait réussi à tricher avec un ordre particulier. @Barrois tu te souviens ?

Barrois, 2022-09-23:
Salut Jody,Tu me pose une colle ***@***.*** tu te souviens ?" !!! Tu évoques un conflit sur I2C entre le la caméra et le PCA 9685 ?En relisant la dernière version  : https://github.com/Barrois/Detecteur-ESP32-Cam-Blob-Detector/blob/main/documentation/CaptureWithoutDelay_save3_7_RxTx_3_vetical_4/CaptureWithoutDelay_save3_7_RxTx_3_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'ai trouvé  le texte qui doit croorespondre à la résolution de ce problème : #include <Adafruit_PWMServoDriver.h>const int PIN_SDA = 1; // port 1 du esp32-cam sur le SDAconst int PIN_SCL = 3; // port 3 du esp32-cam sur le SCLconst int PAN_ID = 0; // Pan sur le port 0 du PCA9685const int TILT_ID = 1; // Tilt sur le port 1 du PCA9685Adafruit_PWMServoDriver pwm = Adafruit_PWMServoDriver();#define SERVOMIN 150 // this is the 'minimum' pulse length count (out of 4096)#define SERVOMAX 600 // this is the 'maximum' pulse length count (out of 4096)Mais qui pose la question ?Bernard BARROIS  15 rue de la revenue 70400 Chenebier tel : 03 84 27 30 19tel : 06 28 13 62 47envoyé : 23 septembre 2022 à 07:51de : Jodaille ***@***.***>à : Barrois/Detecteur-ESP32-Cam-Blob-Detector ***@***.***>cc : Barrois ***@***.***>, Mention ***@***.***>objet : Re: [Barrois/Detecteur-ESP32-Cam-Blob-Detector] Question: usage de I2C (Issue #6) Bonjour,à priori SDA et SCL ne sont accessibles que sur le connecteur de la caméra.pour la dérivation via la nappe de la camera: https://github.com/Barrois/Detecteur-ESP32-Cam-Blob-Detector/tree/main/documentation/FPC_24P_0.5mm_I2C_DerivationBernard pourra confirmer, les connexions caméra/i2c fonctionnent, il restait la partie initialisation/énumération de la caméra sur le bus. Il me semble que lorsque la caméra s'initialise au démarrage de la carte, le "sketch" prends en gros le premier périhpérique sur le bus I2C. De mémoire Bernard avait réussi à tricher avec un ordre particulier. @Barrois tu te souviens ?—Reply to this email directly, view it on GitHub, or unsubscribe.You are receiving this because you were mentioned.Message ID: ***@***.***>

Patriboom, 2022-09-23:
Merci à vous deux,

ce que j'y comprends, c'est que les broches 1 et 3 de la caméra monopolisent I2C, respectivement SDA et SCL.  C'est pourquoi vous avez dérivé la caméra vers une carte où il vous était possible de souder d'autres accès à ces broches du micro-contrôleur.
L'usage de la librairie PWMServoDriver.h est nul (car mis en commentaire), il est donc inutile de l'appeler.

const int PIN_SDA = 1;  // port 1 du esp32-cam sur le SDA
const int PIN_SCL = 3;  // port 3 du esp32-cam sur le SCL

Si c'est bien cela, j'étudierai le plan du ESP32-cam afin de m'y retrouver.

J'ai aussi lu, hier - mais je n'arrive pas à m'inscrire au forum (je ne reçois pas le message de confirmation) - qu'il serait plus simple encore d'y arriver.  Selon [Eurymedon](https://www.esp32.com/viewtopic.php?f=13&t=29342&p=101893&hilit=ai+thinker#p101893), 21 août dernier, il suffirait de fournir une horloge.
Je tenterai de m'incrire au forum sous un autre nom afin d'y accéder enfin et vous reviendrai avec des détails.

Au plaisir et bon succès à vos études des frelons.

Jodaille, 2022-09-23:
Bonjour,

oui en fait nous avons employé deux cartes de ce type: https://fr.aliexpress.com/item/4000099171451.html
pour avoir un connecteur de nappe côté caméra, et un autre avec une nappe "rallonge".
Les deux cartes sont soudées entre-elles.

Cela nous permettait d'avoir accès à SDA/SCL tout en conservant la caméra
et la carte sD moyennant une autre bidouille.
Si je me souviens bien: https://dr-mntn.net/2021/02/using-the-sd-card-in-1-bit-mode-on-the-esp32-cam-from-ai-thinker

Je pense avoir retrouvé un des sketchs concerné: https://github.com/Barrois/Detecteur-ESP32-Cam-Blob-Detector/blob/main/sketchbook/Esp32cam_FFT_Blob_PanTit_I2C_0/Esp32cam_FFT_Blob_PanTit_I2C_0.ino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

Il me semble qu'il faut initialiser l'I2C avec Wire.begin(PIN_SDA, PIN_SCL);
puis ensuite initialiser la caméra.
( Ou l'inverse, il y'a un loup :) )

Si jamais vous êtes d'accord Bernard serait ravi d'échanger avec vous,

Bonne journée.

Patriboom, 2022-09-23:
Mais bien sûr, je serais ravi de d'échanger avec Bernard.
Je suis au Québec, cependant.  Il faut prévoir le décallage

Je vois dans [https://github.com/RuiSantosdotme/ESP32-CAM-eBook/blob/master/Code/Module_4/Video_Streaming_Web_Server_Sensor_Readings/](https://github.com/RuiSantosdotme/ESP32-CAM-eBook/blob/master/Code/Module_4/Video_Streaming_Web_Server_Sensor_Readings/Video_Streaming_Web_Server_Sensor_Readings.ino)
que le I2C_SCL est mis à la terre ( broche 15 du SCP32 [selon les specs de Espressif](https://docs.ai-thinker.com/_media/esp32/docs/esp32_cam_sch.pdf) avez-vous essayé cela ?

Patriboom, 2022-09-23:
Selon [cet auteur](https://microdigisoft.com/esp32-interfacing-multiple-device-using-i2c-bus/), nous devrions pouvoir utiliser n'importe quelle paire de GPIO en guise de I2c SCL / SDA

---------------  début de citation ----------------
_Use Any Pins as I2C with ESP32
We can configure almost any pin of ESP32 board with I2C capabilities using Wire.h library. To use pins with this library, you initialize the I2C using function as given below. So, we just need to set your desired SDA and SCL GPIOs on the I2C_SDA and I2C_SCL variables._

`Wire.begin(I2C_SDA, I2C_SCL);`

---------------  fin de citation ----------------

Je crois que c'est la commande qui manquait à ma programmation et qui m'a amené jusqu'à vous.
Je vous en donnerai des nouvelles.

Patriboom, 2022-09-24:
Et oui, ça fonctionne!
J'ai repris le code de [Rui Santos](https://github.com/RuiSantosdotme/ESP32-CAM-eBook/tree/master/Code/Module_4/Video_Streaming_Web_Server_Sensor_Readings) avec de bons yeux et me suis rappelé avoir lu une consigne relative à l'usage de certaines broches de mise à terre.

Afin de faire fonctionner le tout:  il suffit de NE PAS utiliser la broche 16 (GND), celle immédiatement à côté de GPIO1 (U0TXD )
C'est là-dessus que j'ai perdu des heures!

Le code cité ci-haut semble bien fonctionnel.
Comme le dit la documentation, le signal WiFi de ESP32-CAM est faible  Il faut, par conséquent, garder le module près du routeur WiFi ou faire fonctionner avec une antenne externe.  Pour cela, il y a des consignes à suivre, il ne faut se contenter de connecter la première antenne venue.

Merci de votre attention et des recherches que vous avez faites suite à ma question.
Au plaisir.

Barrois, 2022-09-24:
Salut Patriboom,
J'aimerai discuter un peu avec toi,
de ce que tu fais et pourquoi tu as besoin de ports supplémentaires sur l'Esp-Cam
bernard.barrois@orange.fr

Patriboom, 2022-09-24:
Bonjour Bernard,

	nous pouvons planifier un entretien audio-vidéo si vous le
désirez.

On Sat, 24 Sep 2022 00:47:16 -0700
Barrois ***@***.***> écrivites:

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

---

Soyez artisans de paix.

Patrick Allaire, ptre

Barrois, 2022-09-24:
Ok,
Jody ça te va ?

Envoyé depuis l'application Mail Orange
----------------De : Patriboom ***@***.***>Envoyé : samedi 24 septembre 2022 18:33À : Barrois/Detecteur-ESP32-Cam-Blob-Detector ***@***.***>Cc : Barrois ***@***.***>; Mention ***@***.***>Objet : Re: [Barrois/Detecteur-ESP32-Cam-Blob-Detector] Question: usage de I2C (Issue #6)

Bonjour Bernard,

 nous pouvons planifier un entretien audio-vidéo si vous le

désirez.

On Sat, 24 Sep 2022 00:47:16 -0700

Barrois ***@***.***> écrivites:

> Salut Patriboom,

> J'aimerai discuter un peu avec toi,

> de ce que tu fais et pourquoi tu as besoin de ports supplémentaires

> sur l'Esp-Cam ***@***.***

>

---

Soyez artisans de paix.

Patrick Allaire, ptre

—Reply to this email directly, view it on GitHub, or unsubscribe.You are receiving this because you were mentioned.Message ID: ***@***.***>

Closed 2022-09-24.

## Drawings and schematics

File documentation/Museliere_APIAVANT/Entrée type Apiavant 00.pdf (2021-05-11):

1

B

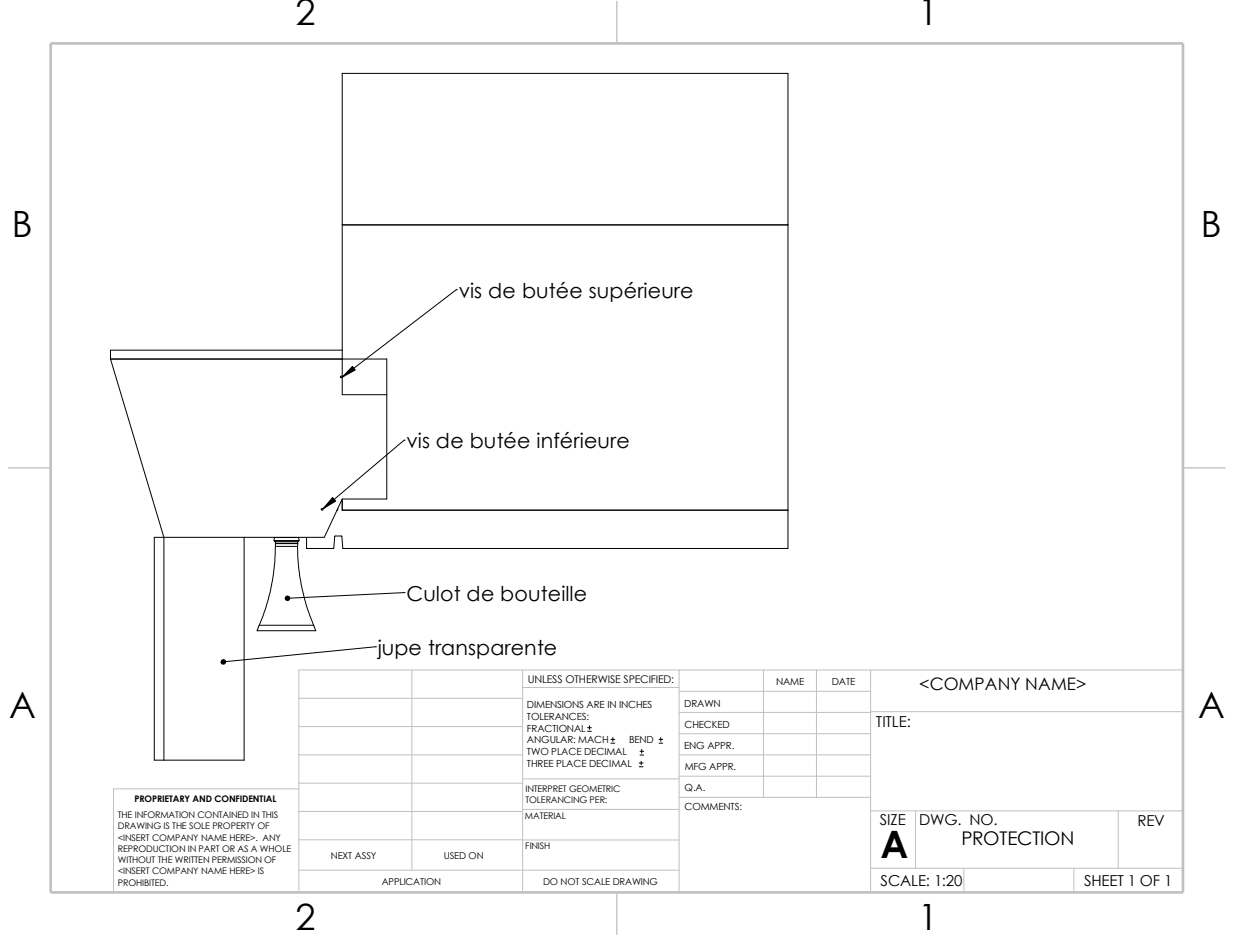
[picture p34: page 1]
BEND; DATE; A DRAWN; COMMENTS:; NAME; <COMPANY NAME>; jupe transparente

vis de butée supérieure

vis de butée inférieure

Culot de bouteille

UNLESS OTHERWISE SPECIFIED:

DIMENSIONS ARE IN INCHES
TOLERANCES:
FRACTIONAL
ANGULAR: MACH
TWO PLACE DECIMAL
THREE PLACE DECIMAL

CHECKED | | TITLE:

ENG APPR.
MFG APPR.

INTERPRET GEOMETRIC TOLERANCING PER: | Q.A.

PROPRIETARY AND CONFIDENTIAL
THE INFORMATION CONTAINED IN THIS
DRAWING IS THE SOLE PROPERTY OF
<INSERT COMPANY NAME HERE>. ANY
REPRODUCTION IN PART OR AS A WHOLE
WITHOUT THE WRITTEN PERMISSION OF
<INSERT COMPANY NAME HERE> IS
PROHIBITED.

NEXT ASSY | | MATERIAL | | SIZE A | DWG. NO. PROTECTION | REV

USED ON | FINISH

APPLICATION | DO NOT SCALE DRAWING | | SCALE: 1:20 | | SHEET 1 OF 1

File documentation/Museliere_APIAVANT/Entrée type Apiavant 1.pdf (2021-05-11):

B

B

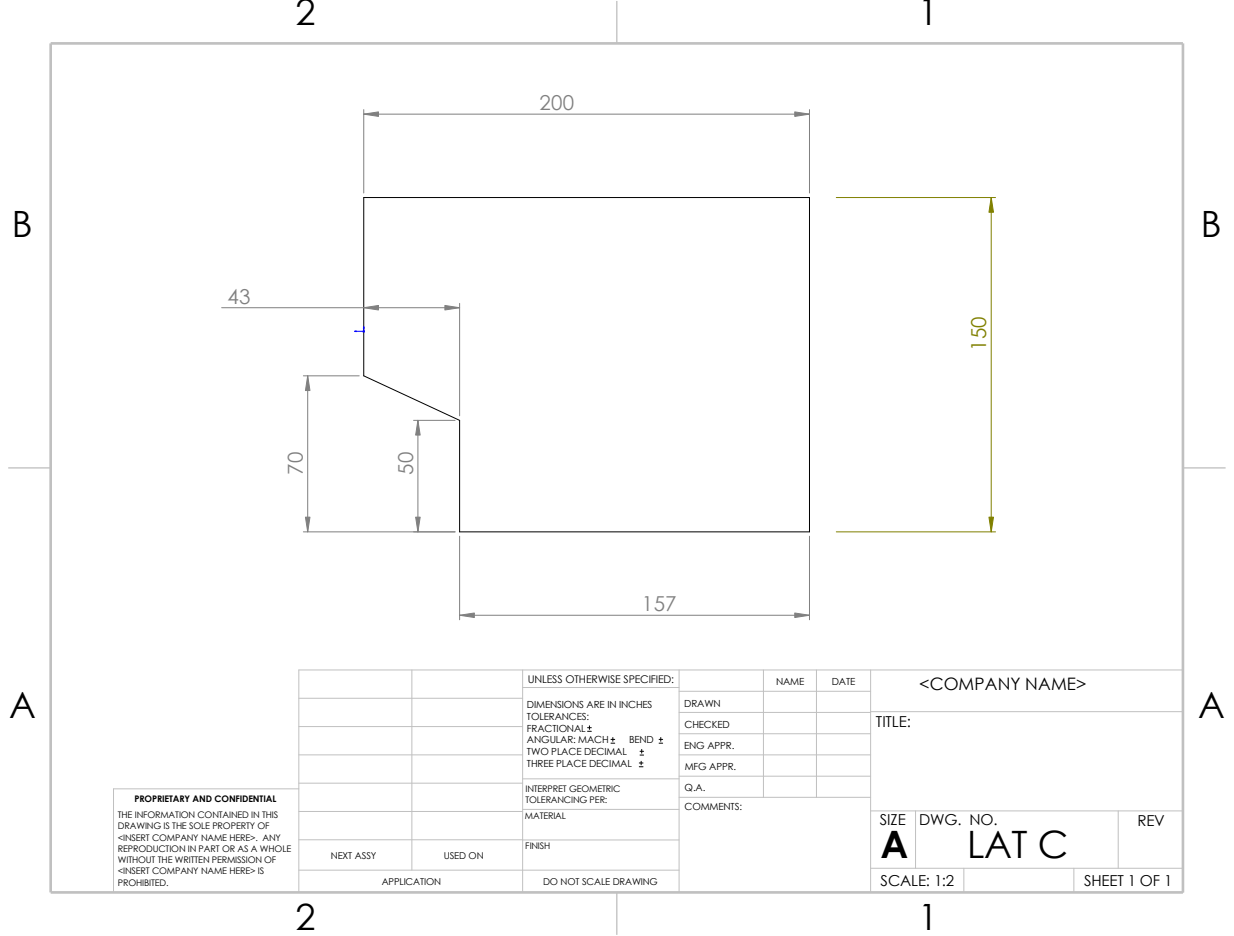
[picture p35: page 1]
BEND; COMMENTS:; PROHIBITED.; SHEET 1 OF 1; APPLICATION; DO NOT SCALE DRAWING; SCALE: 1:2

<COMPANY NAME> ⁷⁰

UNLESS OTHERWISE SPECIFIED: | | NAME | DATE

DRAWN
CHECKED | | | TITLE:

DIMENSIONS ARE IN INCHES
TOLERANCES:
FRACTIONAL
ANGULAR: MACH
TWO PLACE DECIMAL
THREE PLACE DECIMAL

ENG APPR.
MFG APPR.

INTERPRET GEOMETRIC TOLERANCING PER: | Q.A.

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

NEXT ASSY | USED ON | MATERIAL | SIZE A | DWG. NO. LAT C | REV

FINISH

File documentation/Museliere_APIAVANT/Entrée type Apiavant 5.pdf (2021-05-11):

B

2 1

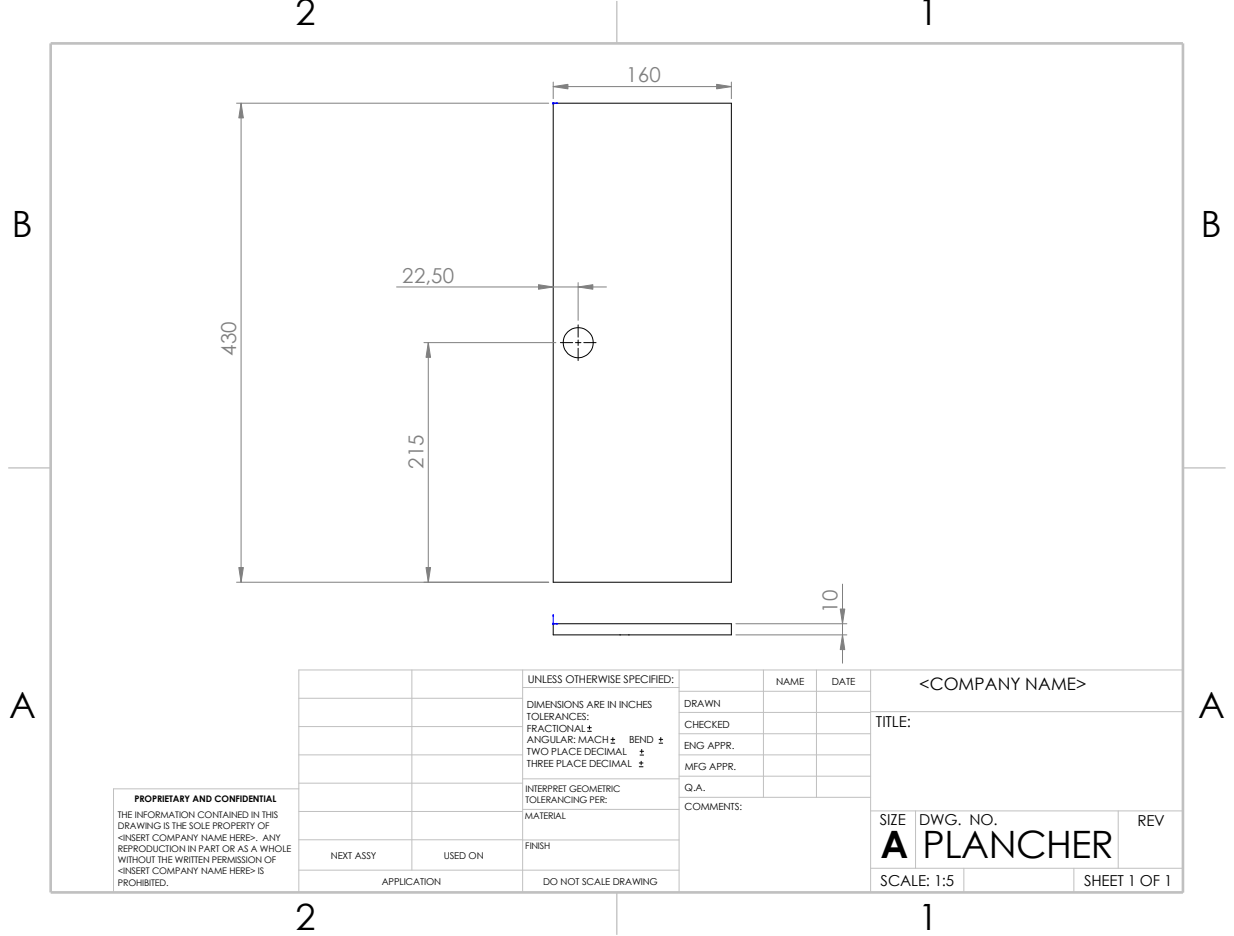
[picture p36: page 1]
APPLICATION; BEND; DATE; A DRAWN; COMMENTS:; PROHIBITED.; SHEET 1 OF 1; NAME; DO NOT SCALE DRAWING; SCALE: 1:5

<COMPANY NAME> ¹⁰ ⁴³⁰

UNLESS OTHERWISE SPECIFIED:

DIMENSIONS ARE IN INCHES
TOLERANCES:
FRACTIONAL
ANGULAR: MACH
TWO PLACE DECIMAL
THREE PLACE DECIMAL

CHECKED | | TITLE:

ENG APPR.
MFG APPR.

INTERPRET GEOMETRIC TOLERANCING PER: | Q.A.

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

NEXT ASSY | USED ON | MATERIAL | SIZE A | DWG. NO. PLANCHER | REV

FINISH

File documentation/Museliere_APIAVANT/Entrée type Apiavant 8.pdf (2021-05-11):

B

B

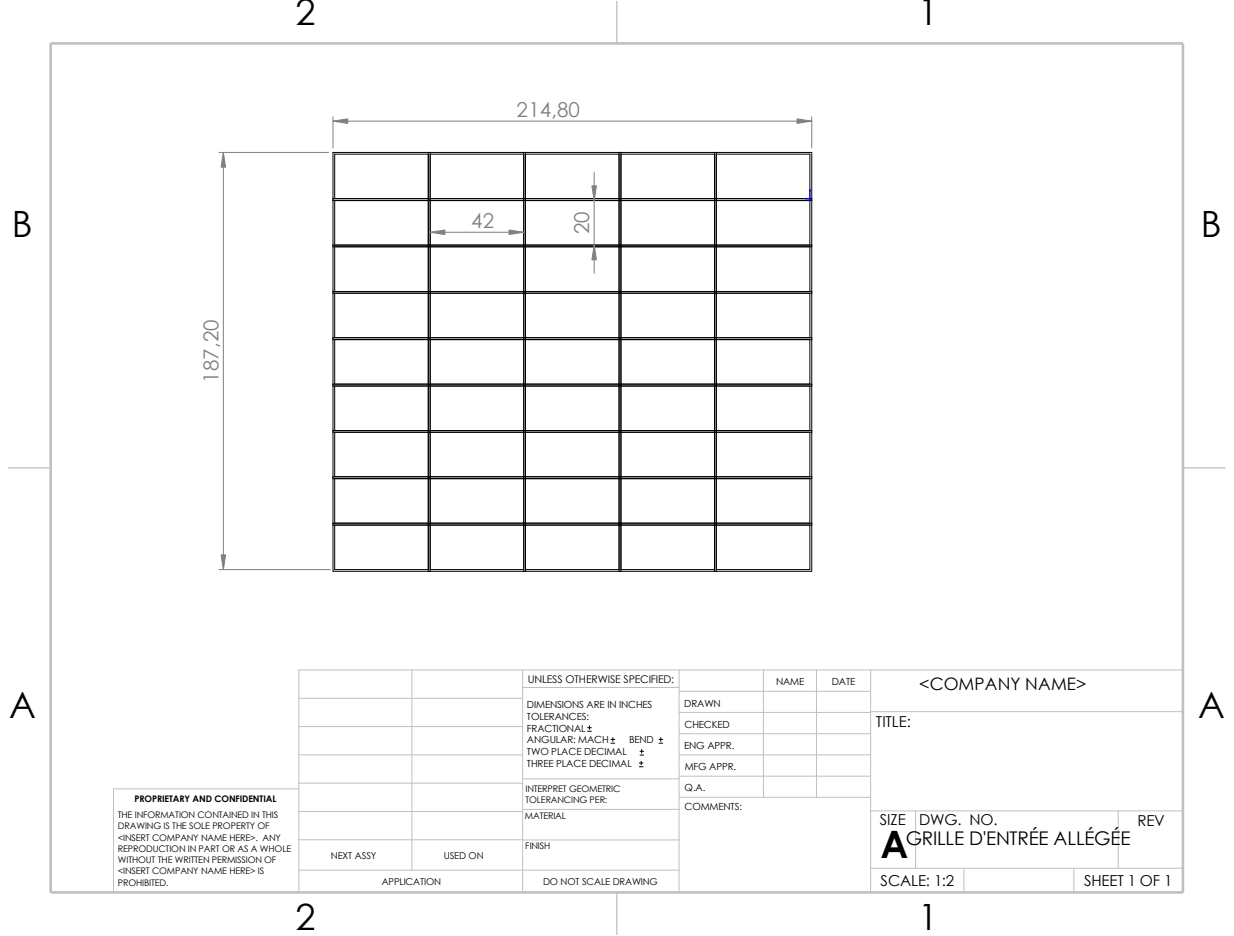
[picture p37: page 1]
BEND; COMMENTS:; PROHIBITED.; SHEET 1 OF 1; APPLICATION; SCALE: 1:2

UNLESS OTHERWISE SPECIFIED: | | NAME | DATE | <COMPANY NAME>

DRAWN
CHECKED | | | TITLE:

DIMENSIONS ARE IN INCHES
TOLERANCES:
FRACTIONAL
ANGULAR: MACH
TWO PLACE DECIMAL
THREE PLACE DECIMAL

ENG APPR.
MFG APPR.

INTERPRET GEOMETRIC TOLERANCING PER: | Q.A.

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

NEXT ASSY | USED ON | MATERIAL | SIZE A GRILLE D'ENTRÉE ALLÉGÉE | DWG. NO. | REV

FINISH

DO NOT SCALE DRAWING

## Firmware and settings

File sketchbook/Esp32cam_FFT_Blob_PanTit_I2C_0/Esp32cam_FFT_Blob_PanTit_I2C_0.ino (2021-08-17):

/*
 * Licensed to the Apache Software Foundation (ASF) under one
or more contributor license agreements.  See the NOTICE file
distributed with this work for additional information
regarding copyright ownership.  The ASF licenses this file
to you under the Apache License, Version 2.0 (the
"License"); you may not use this file except in compliance
with the License.  You may obtain a copy of the License at
  http://www.apache.org/licenses/LICENSE-2.0
Unless required by applicable law or agreed to in writing,
software distributed under the License is distributed on an
"AS IS" BASIS, WITHOUT WARRANTIES OR CONDITIONS OF ANY
KIND, either express or implied.  See the License for the
specific language governing permissions and limitations
under the License.
    https://robotzero.one/time-lapse-esp32-cameras/
 * https://github.com/robotzero1/esp32cam-timelapse/blob/master/timelapse-sd.ino
la logique prévue :
- quand on allume l'esp32-cam
   -0 il lit l'EEProm pour savoir à quel numéro de fichier il en est : xxx
   -1 il fait une localisation qu'il sauvegarde sur la carte SD : fichier LOCAxxx.txt
   -2 il fait une photo sauvegarder sur la carte SD : fichier CAPTURExxx.jpg
   -3 il se mets en position d'écoute sur le port 0
   -4 il fait la FFT
   -5 si la filtre de la FFT est positif, il commence à compter
   -6 si le compteur du filtre atteint 5 reconnaissances en moins d'une seconde
        il collecte les 5 FFT qui ont déclenchées l'alarme et les stocke sur la carte SD : fichier FFTxxx.txt
        puis l'esp32-cam redémarre pour faire la localisation et la photo
   -7 il fait la localisation du blob sur une photo faite en 320x240 et dégradé en 80x60
   -8 il envoie les coordonnées au PCA9685 qui gère le Pan-Tilt
       sur les GPIO 26 SDA et GPIO 27 SCL
   -1-7 sinon il recommence en -4
 */
#define CAMERA_MODEL_AI_THINKER

#include "FS.h"                // SD Card ESP32
#include "SD_MMC.h"            // SD Card ESP32
#include <SPIFFS.h>
#include <EloquentArduino.h>
#include <eloquentarduino/io/serial_print.h>
#include <eloquentarduino/vision/camera/ESP32Camera.h>
#include <eloquentarduino/vision/io/writers/JpegWriter.h>

#define FRAME_SIZE FRAMESIZE_QVGA
#define PIXFORMAT PIXFORMAT_GRAYSCALE
#define W 320
#define H 240
#define w 80 //32
#define h 60 //24
#define DIFF_THRESHOLD 15
#define MOTION_THRESHOLD 0.15

// delete the second definition if you want to turn on code benchmarking
#define timeit(label, code) { uint32_t start = millis(); code; uint32_t duration = millis() - start; eloquent::io::print_all("It took ", duration, " millis for ", label); }
#define timeit(label, code) code;

using namespace Eloquent::Vision;

camera_fb_t *frame;
Camera::ESP32Camera camera(PIXFORMAT);
uint8_t downscaled[w * h];
IO::Decoders::GrayscaleRandomAccessDecoder decoder;
//IO::Decoders::Red565RandomAccessDecoder decoder;
Processing::Downscaling::Center<W / w, H / h> strategy;
Processing::Downscaling::Downscaler<W, H, w, h> downscaler(&decoder, &strategy);
Processing::MotionDetector<w, h> motion;
IO::Writers::JpegWriter<W, H> jpegWriter;

// début partie Son FFT
// Norwegian
// https://www.norwegiancreations.com/2017/08/what-is-fft-and-how-can-you-implement-it-on-an-arduino/
#include "arduinoFFT.h" // Standard Arduino FFT library https://github.com/kosme/arduinoFFT
arduinoFFT FFT = arduinoFFT();
#define SAMPLES 2048             // Must be a power of 2
#define SAMPLING_FREQUENCY 40000 // Hz, must be 40000 or less due to ADC conversion time. Determines maximum frequency that can be analysed by the FFT Fmax=sampleF/2.
#define amplitude 150            // Depending on your audio source level, you may need to increase this value
unsigned int sampling_period_us;
double vReal1[SAMPLES];
double vImag1[SAMPLES];
int bb =55; // nb de frequence qu'on garde
double traceur [275]={0}; // pour sauver les 5 FFT de 55 nombres
double local [10]={0}; // pour sauver les 10 localisations

//    voir l'exemple FFT_01 https://github.com/kosme/arduinoFFT/blob/master/Examples/FFT_01/FFT_01.ino
unsigned long newTime, chrono1, chrono2;
int compteur_tour =0;
int Nb_chrono =0;
// compteur d'attaque
int Cpt_Attaque=0;
#define uS_TO_S_FACTOR 1000000  /* Conversion factor for micro seconds to seconds */
#define TIME_TO_SLEEP  3   // durée du sommeil en secondes ici 900 = 1/4 d'heure

// fin de la partie Son FFT


void capture();
void save();
void stream_downscaled();
void stream();
void initMicroSDCard();
void capture();
void takeSavePhoto(String path);
int angleToPulse(int ang);

unsigned int pictureNumber = 0;
String path;

#include <Wire.h>
#include <Adafruit_PWMServoDriver.h>
const int PIN_SDA = 26;  // port 26 du esp32-cam sur le SDA directement sur la puce
const int PIN_SCL = 27;  // port 27 du esp32-cam sur le SCL directement sur la puce

const int PAN_ID = 0;  // Pan  sur le port 0 du PCA9685
const int TILT_ID = 1; // Tilt sur le port 1 du PCA9685

Adafruit_PWMServoDriver pwm = Adafruit_PWMServoDriver();
#define SERVOMIN  150 // this is the 'minimum' pulse length count (out of 4096)
#define SERVOMAX  600 // this is the 'maximum' pulse length count (out of 4096)
  int angle_pan_1 =4;        // position des bords (inutile)
  int angle_pan_2 =36;
  int angle_til_1 =46;
  int angle_til_2 =78;

  int angle_pan_0 =21;       // position du milieu
  int angle_til_0 =61;

  int angle_pan , angle_til ; // position courante

unsigned long previousMillis = 0;// on stocke le temps de la derniere execution

const long interval = 5000; // intervale entre chaque execution (milliseconds)

void setup() {
  Serial.begin(115200);
  Serial.println(__FILE__);
  SPIFFS.begin(true);
  delay(100);
  Serial.println("Begin");

  //Initialize MicroSD
  Serial.print("Initializing the MicroSD card module... ");
  initMicroSDCard();

  Wire.begin(PIN_SDA, PIN_SCL);
  pwm.begin();
  pwm.setPWMFreq(60);

  camera.begin(FRAME_SIZE);
}

void loop() {

    //
    //   prise de son et création de sa FFT
    //
    for (int i = 0; i < SAMPLES; i++) {
      newTime  = micros();         //  lecture du son via un micro mis en GPIO0
      vReal1[i] = analogRead(0);   //  Using pin number for ADC port ici GPIO0
      vImag1[i] = 0;
      while ((micros() - newTime) < sampling_period_us) { /* do nothing to wait */ }
    }
    FFT.Windowing(vReal1, SAMPLES, FFT_WIN_TYP_HAMMING, FFT_FORWARD);
    FFT.Compute(vReal1, vImag1, SAMPLES, FFT_FORWARD);
    FFT.ComplexToMagnitude(vReal1, vImag1, SAMPLES);

    // calcul du pic
    double pic1 = FFT.MajorPeak(vReal1, SAMPLES, SAMPLING_FREQUENCY);

    //
    // début des tests de frelons asiatiques
    //

    pic1 = 220;  // pour test

    // on cherche si le pic = 234 +- 10%
    if (pic1 >210  && pic1 <=260) {
      // soupçon de frelon => on garde la trace de la FFT
      // enregistrement de la FFT
      Serial.print("debut du vecteur FFT : ");
      Serial.println(Nb_chrono);

      // mise en tableau des 5 parties réelles vecteurs de la FFT
      for (int i = 2; i < bb; i++) { // i = 2 pour éliminer les basses fréquences < 78 Hz
        traceur [Nb_chrono*bb+i] = vReal1 [i];
        Serial.print(traceur [i]);
        Serial.print("  ");
      }
      Serial.println("fin du vecteur FFT");
      //    Serial.println("Computed magnitudes: apres _1 ");
      //    PrintVector(traceur, bb, SCL_FREQUENCY);
      Serial.print("0_Nb_chrono : ");
      Serial.print (Nb_chrono);
      Serial.print(" chrono1 : ");
      Serial.print (chrono1);
      Serial.print(" chrono2 : ");
      Serial.println(chrono2);

      // est-ce que il y a  5 pics en 235 en moins de 30 secondes ?
      chrono2 = millis(); // demarrage du chrono 2
       if (Nb_chrono == 0) {
        chrono1 = chrono2 ;  // remise à l'heure du compteur 1
       }
      unsigned long interval;
      interval = chrono2 - chrono1;
      Serial.print("1_Nb_chrono : ");
      Serial.print (Nb_chrono);
      Serial.print(" chrono1 : ");
      Serial.print (chrono1);
      Serial.print(" interval : ");
      Serial.print (interval);
      Serial.print(" chrono2 : ");
      Serial.println(chrono2);
      if (interval < 5000 ) {     // les deux pics sont séparés de moins de 5s
        chrono1 = chrono2;
        chrono2 = millis();
        Nb_chrono++;
        delay(100); // attente
      } else {
        Nb_chrono = 0; // remise à zero du compteur
      }
      Serial.print("2_Nb_chrono : ");
      Serial.print (Nb_chrono);
      Serial.print(" chrono1 : ");
      Serial.print (chrono1);
      Serial.print(" interval : ");
      Serial.print (interval);
      Serial.print(" chrono2 : ");
      Serial.println(chrono2);
      if ( Nb_chrono > 4 ) {     // !!!! FRELON !!!!
         Nb_chrono=0;
        // affichage alerte  FRELON !
        Serial.println("  A L E R T E ");
        Serial.println(" F R E L O N S");
        Serial.println("   /-------!  ");
        Serial.println("   !  o-o  !  ");
        Serial.println("   !  (!)  ! ");
        Serial.println("   !___!___/  ");

        //  save_FFT_numbered(); // si on veut sauvegarder les 5 FFT
        //
        //  fin de la prise de son et création de sa FFT
        //
      }
    } // fin des tests son
    pwm.setPWM(PAN_ID,  0, angleToPulse(angle_pan_1));
    pwm.setPWM(TILT_ID, 0, angleToPulse(angle_til_1));
    capture();

    //Path where new picture will be saved in SD Card
    path = "/picture" + String(pictureNumber) +".jpg";
    Serial.printf("Picture file name: %s\n", path.c_str());
    //Take and Save Photo
    takeSavePhoto(path);
    pictureNumber++;
    delay(100);

 // while(1);
}

 void capture() {
  timeit("capture frame", frame = camera.capture());
  // scale image from size H * W to size h * w
  timeit("downscale", downscaler.downscale(frame->buf, downscaled));

  eloquent::io::print_all("START OF BERNARD");

  int ind1=0;
  Serial.println("tableau i = w , j = h");
  for(int i = 0; i < h; i++) {
    for(int j = 0; j < w; j++) {
      ind1 ++;
      Serial.print(downscaled[ind1]);
      Serial.print(";");
    }
    Serial.println();
  }
  // bornes de fenétrage
  int by1 = 22; //    9; 80/32*9
  int by2 = 47; //   19;
  int bx1 = 45; //   15;
  int bx2 = 60; //   20;
  int noir = 255;
  int ix_noir, iy_noir , ind_noir;
  int ind2;

  Serial.print(" le point de depart est : ");
  Serial.print(ind2);
  Serial.print(" :  ");
  Serial.print(by1);
  Serial.print(" , ");
  Serial.println(bx1);

  for(int i = by1; i < by2; i++) {
    ind2 = (i-1) * w + bx1 ; // decalage d'un rang
    for(int j = bx1; j < bx2; j++) {
    /*
     Serial.print(" le point courant : ");
     Serial.print(ind2);
     Serial.print(" noir = ");
     Serial.print(downscaled[ind2]);
     Serial.print("  : x = ");
     Serial.print(i);
     Serial.print(" , y =  ");
     Serial.println(j);
    */
      // recherche du plus noir
      if ( noir > downscaled[ind2]){
        noir = downscaled[ind2];
        iy_noir = i;
        ix_noir = j;
        ind_noir = ind2;
      }
      Serial.print(" le plus noir est : ");
      Serial.print(noir);
      Serial.print(" en : ");
      Serial.print(ind_noir);
      Serial.print("  : y = ");
      Serial.print(iy_noir);
      Serial.print(" , x =  ");
      Serial.println(ix_noir);

      ind2++;
    }
  }
  // la on a le y, x du plus noir
  // il faut transformer les y,x en angle pour le Pan-Tilt
  // point central = y,x = 25,30 => pan, tilt = 21,61
  // y = - 32/52 +   x = + 32/52 pour une photo en  80x60

  angle_pan  = angle_pan_0 - (32/52)* iy_noir ;
  angle_til = angle_til_0 +- (32/52)* ix_noir ;
  Serial.print("       Pan   angle " );
  Serial.println(angle_pan);
  Serial.print("      Tilt   angle " );
  Serial.println(angle_til);
  pwm.setPWM(PAN_ID,  0, angleToPulse(angle_pan));
  pwm.setPWM(TILT_ID, 0, angleToPulse(angle_til));
  delay (500);
}

void save() {
  File imageFile = SPIFFS.open("/capture.jpg", "wb");
  uint8_t quality = 30;

  eloquent::io::print_all("The image will be saved as /capture.jpg");
  jpegWriter.write(imageFile, frame->buf, PIXFORMAT, quality);

  eloquent::io::print_all("Saved");

  // Save picture to microSD card

  //Path where new picture will be saved in SD Card
  String path = "/picture" + String(pictureNumber) +".jpg";
  Serial.printf("Picture file name: %s\n", path.c_str());

  fs::FS &fs = SD_MMC;
  File file = fs.open(path.c_str(), FILE_WRITE);
  if(!file){
    Serial.println("Failed to open file in writing mode");
  }
  else {
   // file.write(frame->buf, frame->len); // payload (image), payload length
    file.write(imageFile);
    Serial.printf("Saved file to path: %s\n", path.c_str());
  }
  file.close();
  imageFile.close();
  pictureNumber++;
  delay(100);


}

void stream() {
    eloquent::io::print_all("START OF FRAME");
    jpegWriter.write(Serial, frame->buf, PIXFORMAT, 30);
    eloquent::io::print_all("END OF FRAME");
}

void stream_downscaled() {
    eloquent::io::print_all("START OF DOWNSCALED");
    eloquent::io::print_array(downscaled, w * h);
    eloquent::io::print_all("END OF DOWNSCALED");

   //   pour ecrire le fichier a exploiter avec excel

}
void initMicroSDCard(){
  // Start Micro SD card
  Serial.println("Starting SD Card");
  if(!SD_MMC.begin()){
    Serial.println("SD Card Mount Failed");
    return;
  } else {
    Serial.println("SD Card Mount OK");
  }
  uint8_t cardType = SD_MMC.cardType();
  if(cardType == CARD_NONE){
    Serial.println("No SD Card attached");
    return;
  } else {
    Serial.println("SD Card attached OK");
  }
}

void takeSavePhoto(String path){
  // Take Picture with Camera
  camera_fb_t  * fb = esp_camera_fb_get();

  if(!fb) {
    Serial.println("Camera capture failed");
    return;
  }

  // Save picture to microSD card
  fs::FS &fs = SD_MMC;
  File file = fs.open(path.c_str(), FILE_WRITE);
  if(!file){
    Serial.println("Failed to open file in writing mode");
  }
  else {
    uint8_t *jpeg;
    size_t len;
    if (fmt2jpg(frame->buf, W * H, W, H, PIXFORMAT, 30, &jpeg, &len)) {
      file.write(jpeg, len);
      Serial.printf("Saved file to path: %s\n", path.c_str());
      free(jpeg);
    }
    else {
      Serial.println("Not saved");
    }

  }
  file.close();

  //return the frame buffer back to the driver for reuse
  esp_camera_fb_return(fb);
}

int angleToPulse(int ang){
   int pulse = map(ang,00, 180, SERVOMIN,SERVOMAX);// map angle of 0 to 180 to Servo min and Servo max
   Serial.print("Angle: ");Serial.print(ang);
   Serial.print(" pulse: ");Serial.println(pulse);
   return pulse;
}

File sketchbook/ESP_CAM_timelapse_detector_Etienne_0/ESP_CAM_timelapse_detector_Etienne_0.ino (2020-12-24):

/*
Licensed to the Apache Software Foundation (ASF) under one
or more contributor license agreements.  See the NOTICE file
distributed with this work for additional information
regarding copyright ownership.  The ASF licenses this file
to you under the Apache License, Version 2.0 (the
"License"); you may not use this file except in compliance
with the License.  You may obtain a copy of the License at

  http://www.apache.org/licenses/LICENSE-2.0

Unless required by applicable law or agreed to in writing,
software distributed under the License is distributed on an
"AS IS" BASIS, WITHOUT WARRANTIES OR CONDITIONS OF ANY
KIND, either express or implied.  See the License for the
specific language governing permissions and limitations
under the License.
*/
/* https://robotzero.one/time-lapse-esp32-cameras/
 * https://github.com/robotzero1/esp32cam-timelapse/blob/master/timelapse-sd.ino
 */
#include "esp_camera.h"
#include "esp_timer.h"
//#include <WiFi.h>
#include "Arduino.h"
// MicroSD
#include "driver/sdmmc_host.h"
#include "driver/sdmmc_defs.h"
#include "sdmmc_cmd.h"
#include "esp_vfs_fat.h"

#include <EEPROM.h>            // read and write from flash memory
// define the number of bytes you want to access
#define EEPROM_SIZE 1
int file_number;

int capture_interval = 5000; // microseconds between captures

static esp_err_t cam_err;
static esp_err_t card_err;

// CAMERA_MODEL_AI_THINKER
#define PWDN_GPIO_NUM     32
#define RESET_GPIO_NUM    -1
#define XCLK_GPIO_NUM      0
#define SIOD_GPIO_NUM     26
#define SIOC_GPIO_NUM     27
#define Y9_GPIO_NUM       35
#define Y8_GPIO_NUM       34
#define Y7_GPIO_NUM       39
#define Y6_GPIO_NUM       36
#define Y5_GPIO_NUM       21
#define Y4_GPIO_NUM       19
#define Y3_GPIO_NUM       18
#define Y2_GPIO_NUM        5
#define VSYNC_GPIO_NUM    25
#define HREF_GPIO_NUM     23
#define PCLK_GPIO_NUM     22

// Norwegian
// https://www.norwegiancreations.com/2017/08/what-is-fft-and-how-can-you-implement-it-on-an-arduino/
#include "arduinoFFT.h" // Standard Arduino FFT library https://github.com/kosme/arduinoFFT
arduinoFFT FFT = arduinoFFT();
#define SAMPLES 2048             // Must be a power of 2
#define SAMPLING_FREQUENCY 40000 // Hz, must be 40000 or less due to ADC conversion time. Determines maximum frequency that can be analysed by the FFT Fmax=sampleF/2.
#define amplitude 150            // Depending on your audio source level, you may need to increase this value
unsigned int sampling_period_us;
double vReal1[SAMPLES];
double vImag1[SAMPLES];
int bb =55; // nb de frequence qu'on garde
double traceur [275]={0}; // pour sauver les 5 FFT de 55 nombres
/*
//   tracer de la FFT  voir l'exemple FFT_01
#define SCL_FREQUENCY 0x02
#define SCL_INDEX 0x00
#define SCL_TIME 0x01
#define SCL_FREQUENCY 0x02
#define SCL_PLOT 0x03
*/

//    voir l'exemple FFT_01 https://github.com/kosme/arduinoFFT/blob/master/Examples/FFT_01/FFT_01.ino
unsigned long newTime, chrono1, chrono2;
int compteur_tour =0;
int Nb_chrono =0;
// compteur d'attaque
int Cpt_Attaque=0;

// relai en GPIO 16
#define Relai_Ext 16

#define uS_TO_S_FACTOR 1000000  /* Conversion factor for micro seconds to seconds */
#define TIME_TO_SLEEP  3   // durée du sommeil en secondes ici 900 = 1/4 d'heure

void setup() {
    // initialize EEPROM with predefined size
  EEPROM.begin(EEPROM_SIZE);
  file_number = EEPROM.read(0) + 1;

  Serial.begin(115200);
  Serial.println(__FILE__);
  pinMode(0, INPUT);  // entrée son sur GPIO 0
  camera_config_t config;
  config.ledc_channel = LEDC_CHANNEL_0;
  config.ledc_timer = LEDC_TIMER_0;
  config.pin_d0 = Y2_GPIO_NUM;
  config.pin_d1 = Y3_GPIO_NUM;
  config.pin_d2 = Y4_GPIO_NUM;
  config.pin_d3 = Y5_GPIO_NUM;
  config.pin_d4 = Y6_GPIO_NUM;
  config.pin_d5 = Y7_GPIO_NUM;
  config.pin_d6 = Y8_GPIO_NUM;
  config.pin_d7 = Y9_GPIO_NUM;
  config.pin_xclk = XCLK_GPIO_NUM;
  config.pin_pclk = PCLK_GPIO_NUM;
  config.pin_vsync = VSYNC_GPIO_NUM;
  config.pin_href = HREF_GPIO_NUM;
  config.pin_sscb_sda = SIOD_GPIO_NUM;
  config.pin_sscb_scl = SIOC_GPIO_NUM;
  config.pin_pwdn = PWDN_GPIO_NUM;
  config.pin_reset = RESET_GPIO_NUM;
  config.xclk_freq_hz = 20000000;
  config.pixel_format = PIXFORMAT_JPEG;
  //init with high specs to pre-allocate larger buffers
  if (psramFound()) {
    config.frame_size = FRAMESIZE_UXGA;
    config.jpeg_quality = 10;
    config.fb_count = 2;
  } else {
    config.frame_size = FRAMESIZE_SVGA;
    config.jpeg_quality = 12;
    config.fb_count = 1;
  }
  // camera init
  cam_err = esp_camera_init(&config);
  if (cam_err != ESP_OK) {
    Serial.printf("Camera init failed with error 0x%x", cam_err);
    return;
  }
  // SD camera init
  card_err = init_sdcard();
  if (card_err != ESP_OK) {
    Serial.printf("SD Card init failed with error 0x%x", card_err);
    return;
  }
  sampling_period_us = round(1000000 * (1.0 / SAMPLING_FREQUENCY));
  pinMode(Relai_Ext, OUTPUT);

  // prise d'une photo
   save_photo_numbered();
}

static esp_err_t init_sdcard(){
  esp_err_t ret = ESP_FAIL;
  sdmmc_host_t host = SDMMC_HOST_DEFAULT();
  sdmmc_slot_config_t slot_config = SDMMC_SLOT_CONFIG_DEFAULT();
  esp_vfs_fat_sdmmc_mount_config_t mount_config = {
    .format_if_mount_failed = false,
    .max_files = 1,
  };
  sdmmc_card_t *card;

  Serial.println("Mounting SD card...");
  ret = esp_vfs_fat_sdmmc_mount("/sdcard", &host, &slot_config, &mount_config, &card);

  if (ret == ESP_OK) {
    Serial.println("SD card mount successfully!");
  }  else  {
    Serial.printf("Failed to mount SD card VFAT filesystem. Error: %s", esp_err_to_name(ret));
  }
}

static esp_err_t save_photo_numbered(){
  Serial.print("Taking picture: ");
  Serial.println(file_number);
  delay(1000);
  camera_fb_t *fb = esp_camera_fb_get();

  //char *filename = (char*)malloc(21 + sizeof(int));
  char *filename = (char*)malloc(21 + sizeof(file_number));
  sprintf(filename, "/sdcard/capture_%d.jpg", file_number);

  Serial.println(filename);
  FILE *file = fopen(filename, "w");
  if (file != NULL)  {
    size_t err = fwrite(fb->buf, 1, fb->len, file);
    Serial.printf("File saved: %s\n", filename);
  }  else  {
    Serial.println("Could not open file");
  }
  fclose(file);
  esp_camera_fb_return(fb);
  free(filename);
}

static esp_err_t save_FFT_numbered(){
  Serial.print("Taking FFT: ");
  Serial.println(file_number);
  char *filename = (char*)malloc(21 + sizeof(file_number));
  sprintf(filename, "/sdcard/FFT_%d.txt", file_number);
  Serial.println(filename);
  FILE *file = fopen(filename, "w");
  if (file != NULL) {
    for (int i = 0; i < 5*bb; i++) { // 500 = 100 * 5
      char x_buffer[20];
      dtostrf(traceur[i], 5,1, x_buffer);
      fprintf(file,x_buffer);
      fprintf(file,";");
    }
  }
  else {
    Serial.println("Could not open file");
  }
  fclose(file);
  free(filename);
}
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

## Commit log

2020-11-18 Add files via upload
    Nouvelle version avec la licence et une autre approche des MCU pour faciliter la localisation du Blob
2020-12-24 add note laser
2020-12-26 Create Fichier son frelons asiatiques
    Vous trouverez ici des fichiers sons de 2019 qui nous ont servi pour mettre au point le premier détecteur validé en 2020
2021-04-30 add print_ln
2021-05-03 add I2C scanner Spiffs verif
2021-05-11 Add files via upload
    PCB de Michel :
    - 1 - pour la surveillance via un microphone : TONE5-2170.pdf
    - 2 - pour le viseur laser et tir automatique : LASER1171.pdf
2021-05-11 move apiavant doc
    [Protection plancher Nicot beelaz V3 - Bouteille eau coupée-1.STL, Protection plancher Nicot beelaz V3 - Cale 50x40x10^Protection plancher Nicot beelaz V3-6.STL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]
2021-05-11 rename dir
    [Protection plancher Nicot beelaz V3 - Bouteille eau coupée-1.STL, Protection plancher Nicot beelaz V3 - Cale 50x40x10^Protection plancher Nicot beelaz V3-6.STL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]
2021-05-11 Schema Module Laser created-by Michel Lehmann
2021-05-11 start Michel Module Tone with KiCad
    [ModuleTone.kicad_pcb, ModuleTone.sch]
2021-05-11 small step drawing Michel Module TOne
    [ModuleTone.sch]
2021-05-25 Create correspondance entre Photo et Angles de tir
2021-06-08 deplaement servo
2021-06-08 Add files via upload
    Il s'agit du test d'utilisation de broches I2C directement reliées à la puce Esp32 (patte 26 et 27)
2021-08-16 add schema ESP32 i2C cmaera
2021-08-23 deviation i2C camera avec FPC
2021-08-28 I2C pinouts
2021-08-28 add readme deviation I2C
2021-08-28 correction schema I2C / FPC
2021-10-27 Update README.md
    L'objectif est de faire un détecteur bas coût avec la possibilité d'ajuster la détection en fonction du frelon asiatique.
    En effet le poids et la taille du frelon asiatique varient avec l'avancée de la saison et l'abondance de la nourriture,
    ce qui entraine des variations du pic de détection qu'il faut pouvoir régler in situ, d'où ce montage avec un potentiomètre.
2021-10-27 ESP32 spectrum potard
2023-09-30 ESP_CAM_FFT_photo_sd_card_1
    Utilise la FFT pour déclencher la prise d'une photo qui est stockée sur la carte SD
    le test est 5 fois le pic de la FFT est compris entre 210 et 260 Hz
